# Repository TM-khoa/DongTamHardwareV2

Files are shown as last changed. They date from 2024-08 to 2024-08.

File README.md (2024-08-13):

# Hardware Air Cleaning Machine Valve Controller
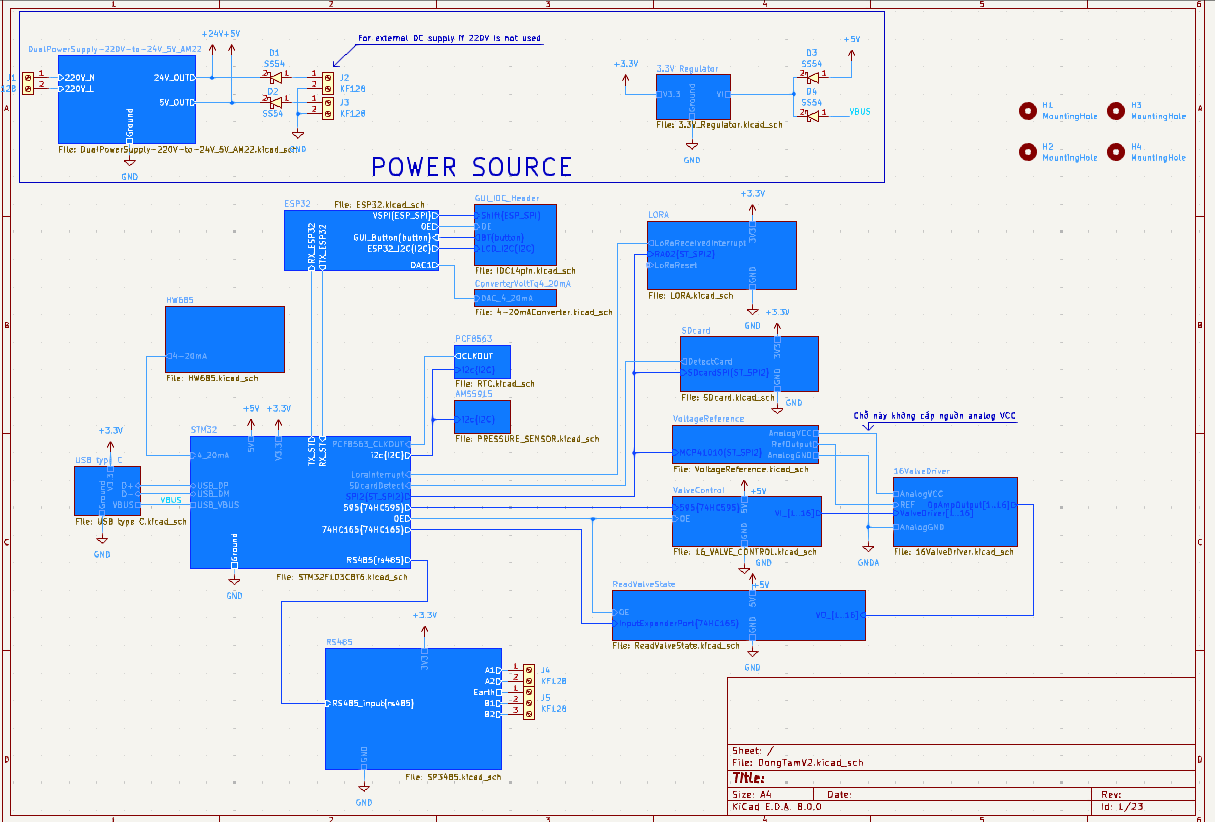
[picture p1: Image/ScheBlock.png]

# Hardware library

Download hardware library at this [repository](https://github.com/TM-khoa/KicadHardwareLibrary.git)
# Hardware description
## Powersource
- The system board is powered by a dual power supply, the AM22 AC-DC converter, which outputs both 24VDC and 5VDC.
- The power for the MCUs, LoRa module, and RS485 needs to be regulated to 3.3V using the LD1117-3.3 regulator.
- Other components can use the 5V output from the AM22.
- Two terminals—one for 5V and one for 24V—can be used to power the system board from an external DC supply.

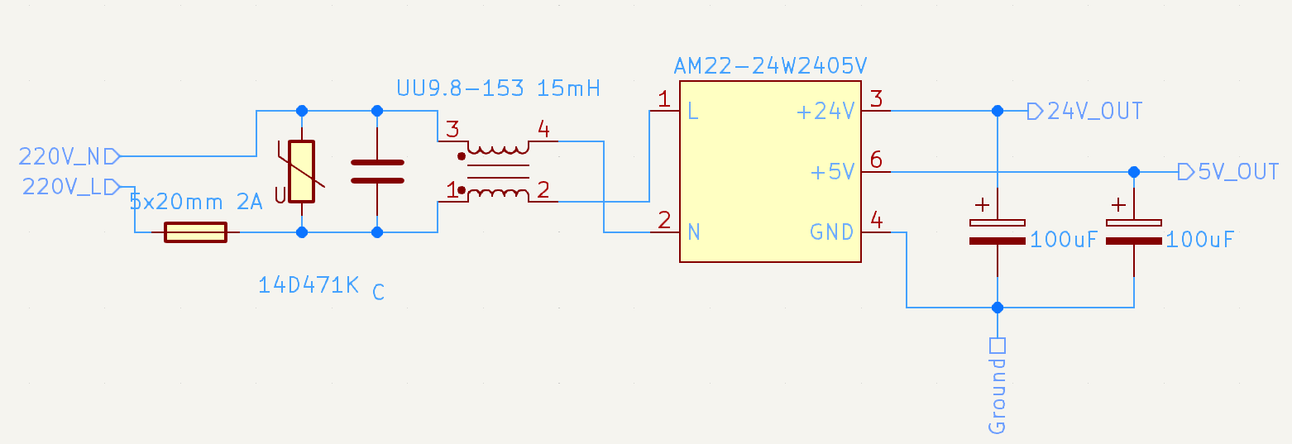
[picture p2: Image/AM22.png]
am22


## Control valve and fault detect
Each output pin of the Output Expander 74HC595 is connected to the Gate pin of an N-channel MOSFET (SI2302). The Source pin is connected to a 0.5 Ohm shunt resistor and to ground, while the Drain pin is connected to one terminal of the valve. The other valve terminal is connected to the 24V power supply.
	
An LM324 Op-Amp samples the voltage drop across the shunt resistor (approximately 300mV). This voltage is compared to a reference voltage to detect faults. A valve error occurs if there is no voltage drop.

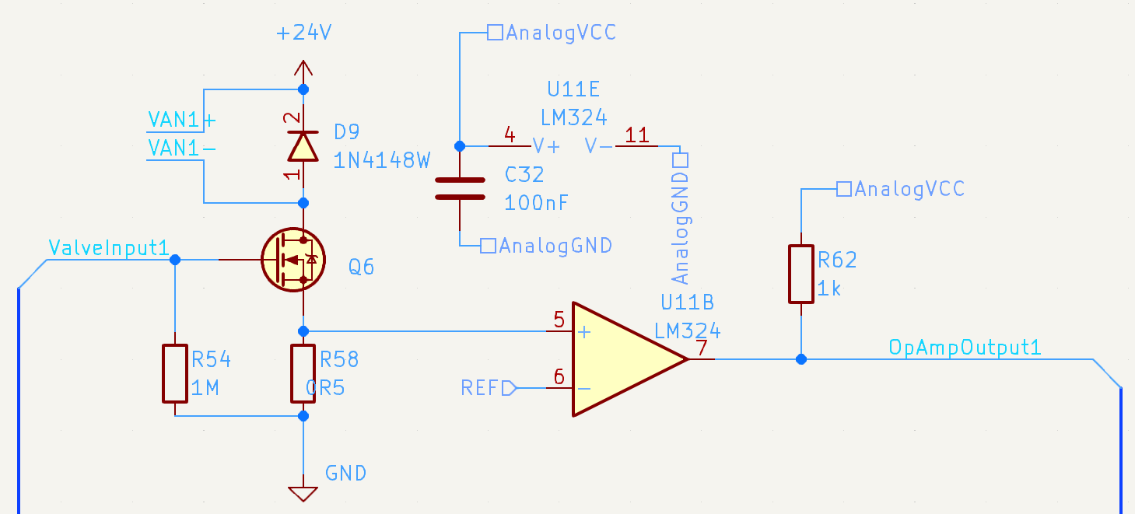
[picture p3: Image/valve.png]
valve


To control 16 valves, two cascaded 74HC595 output expanders are required, with each output pin equipped with an indicator LED.

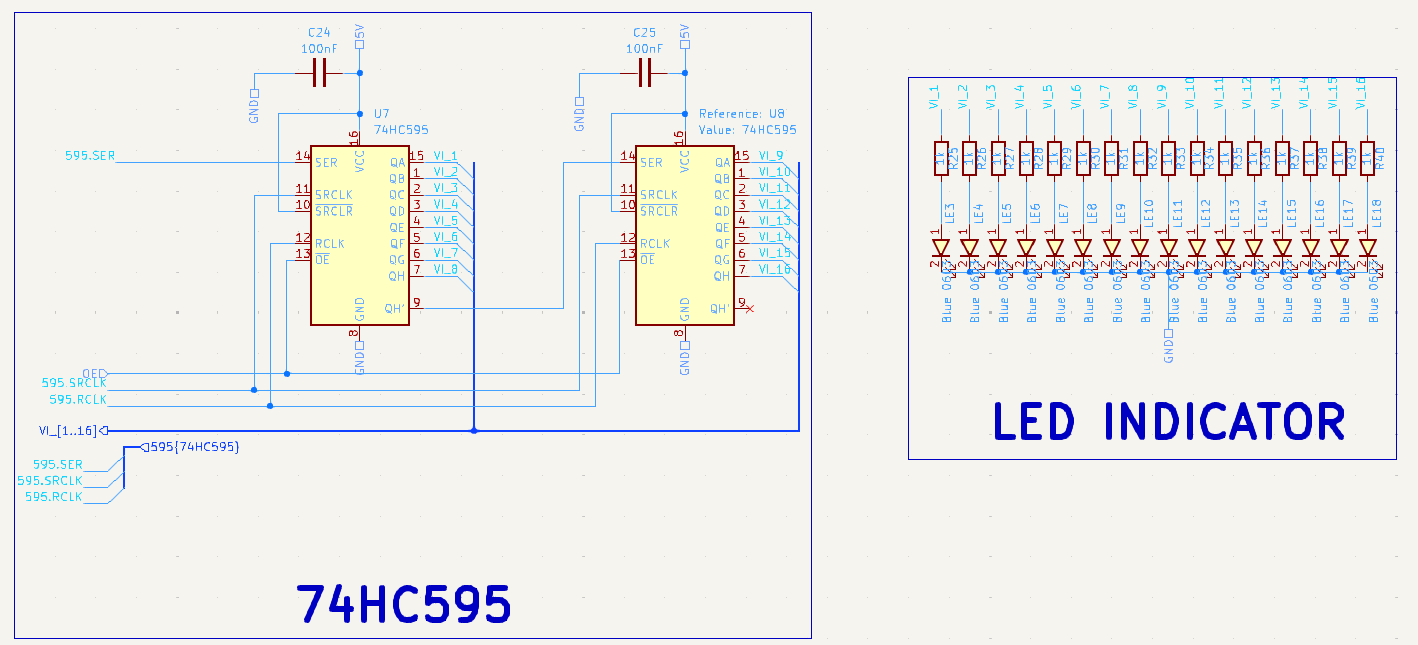
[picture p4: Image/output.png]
output


Each LM324 has four output pins, so four LM324 ICs are needed to monitor up to 16 valves. These outputs are connected to two cascaded 74HC165 input expanders and fed back to the MCU.

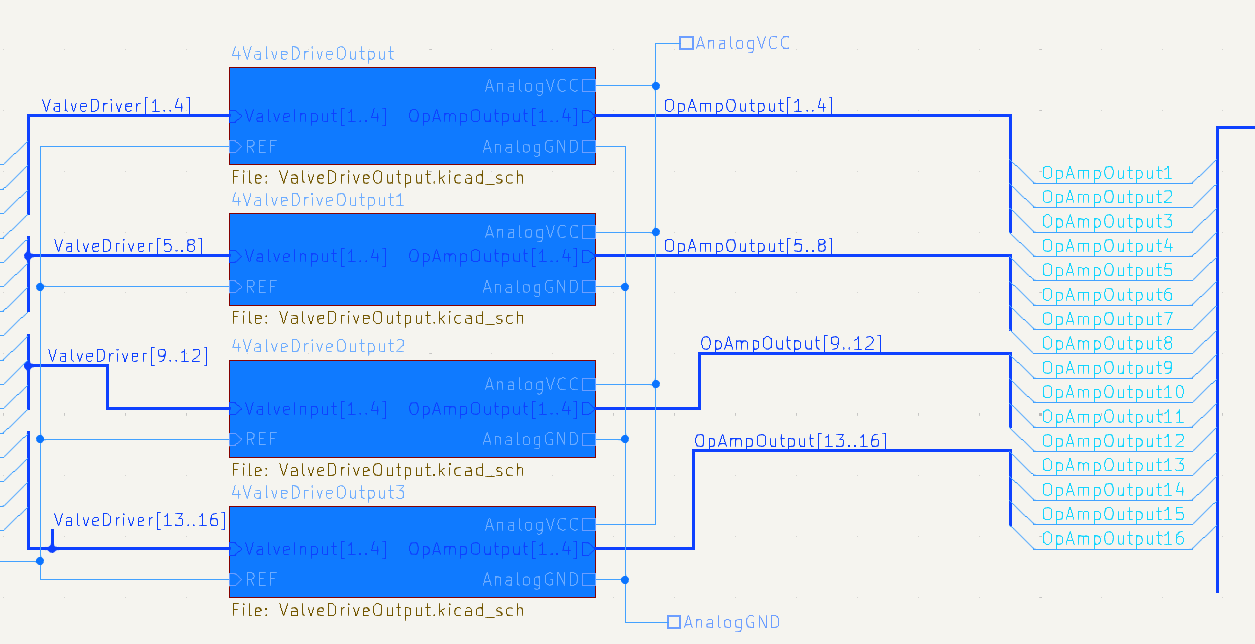
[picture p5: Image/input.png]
input


## Control LCD and LED bar

To interface the PCF8574 and 74HC595 pins (which require 5V at VIH) with the ESP32 (which outputs 3.3V at VOH), logic level shifters are needed on the I2C pins and the 74HC595 GPIO pins.

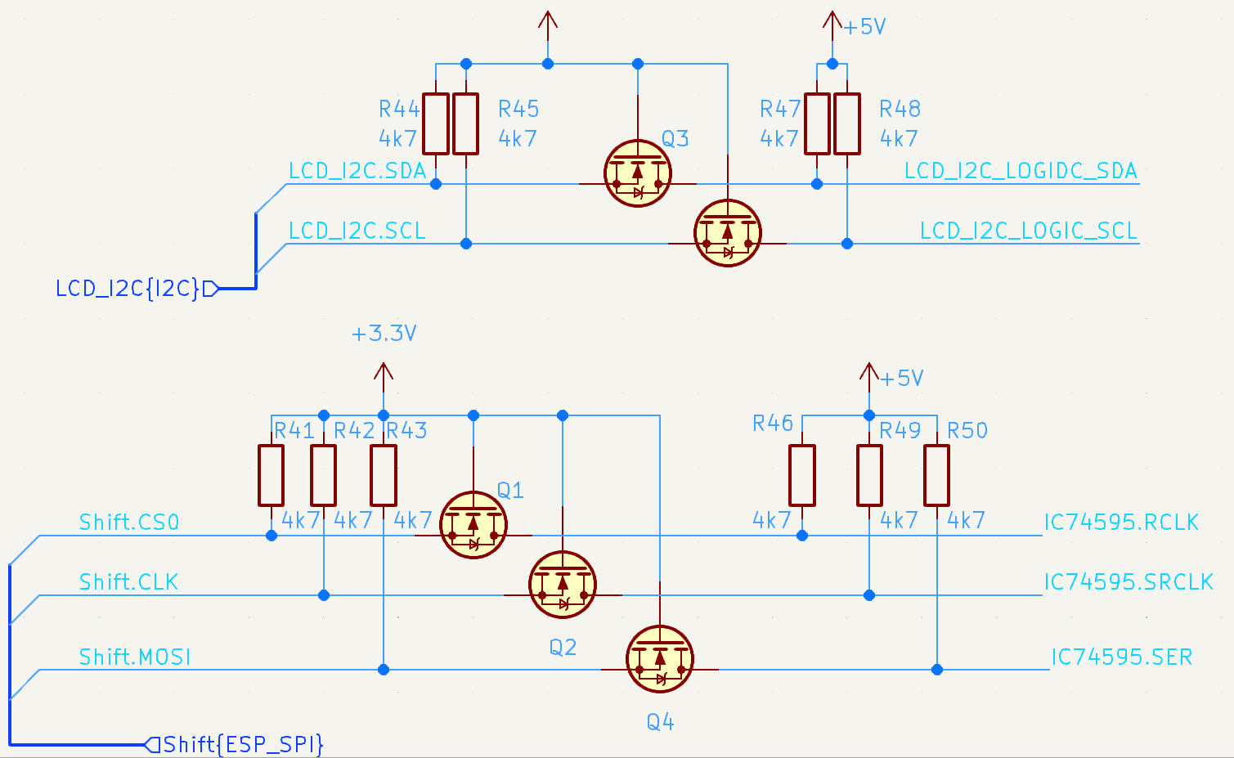
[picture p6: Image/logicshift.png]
logicshift
  

# STM32 pin table
| Pin Number | Pin Name | Function | Device | Description |
|---|---|---|---|---|
| 2 | PC13 | GPIO_OUTPUT | LED | |
| 3 | PC14 | GPIO_INTERRUPT | PCF8563 | Clock input interrupt |
| 18 | PB0 | GPIO_INTERRUPT | LORA RA-02  | LORA interrupt |
| 10 | PA0 | GPIO_OUTPUT | LORA RA-02  | SPI2 Chip select |
| 31 | PA10 | GPIO_OUTPUT | SDcard | SPI2 Chip select |
| 25 | PB12 | GPIO_OUTPUT | MCP41010 | SPI2 Chip select |
| 26 | PB13 | SPI2_SCK | LORA RA-02, Sdcard, MCP41010 | |
| 27 | PB14 | SPI2_MISO | | |
| 28 | PB15 | SPI2_MOSI | | |
| 21 | PB10 | UART3_TX | PC | Log output data to desktop |
| 22 | PB11 | UART3_RX | | |
| 45 | PB8 | I2C1_SCL | PCF8563, AMS5915 | |
| 46 | PB9 | I2C1_SDA | | |
| 42 | PB6 | USART1_TX | ESP32 | |
| 43 | PB7 | USART1_RX | | |
| 11 | PA1 | GPIO_OUTPUT | | |
| 12 | PA2 | USART2_TX | SP3485 | RS485 communicate |
| 13 | PA3 | USART2_RX | | |
| 32 | PA11 | USB_DM | USB-C port  | |
| 32 | PA12 | USB_DP | | |
| 15 | PA5 | GPIO_OUTPUT | 74HC595 | OutputExpander |
| 16 | PA6 | GPIO_OUTPUT | | |
| 17 | PA7 | GPIO_OUTPUT | | |
| 39 | PB3 | GPIO_OUTPUT | 74HC165 | InputExpander |
| 40 | PB4 | GPIO_OUTPUT | | |
| 41 | PB5 | GPIO_INPUT | | |
| 19 | PB1 | ADC | HW685 | Read pressure from SP100 |

# ESP32 pin table

| Pin Number | Pin Name | Function | Device | Description |
|---|---|---|---|---|
| 33 | IO21 | I2C_SDA | PCF8574 | LCD20x4 Output Expander |
| 36 | IO22 | I2C_SCL | | |
| 27 | IO16 | UART_RX | STM32 | |
| 28 | IO17 | UART_TX | | |
| 4 | IO36 | GPIO_INPUT | | Button from GUI user interface module |
| 5 | IO39 | GPIO_INPUT | | |
| 6 | IO34 | GPIO_INPUT | | |
| 7 | IO35 | GPIO_INPUT | | |
| 29 | IO5 | GPIO_OUTPUT| | |
| 30 | IO18 | SPI_CLK | 74HC595 | Control LED bar level |
| 31 | IO19 | SPI_MISO | | |
| 37 | IO23 | SPI_MOSI | | |

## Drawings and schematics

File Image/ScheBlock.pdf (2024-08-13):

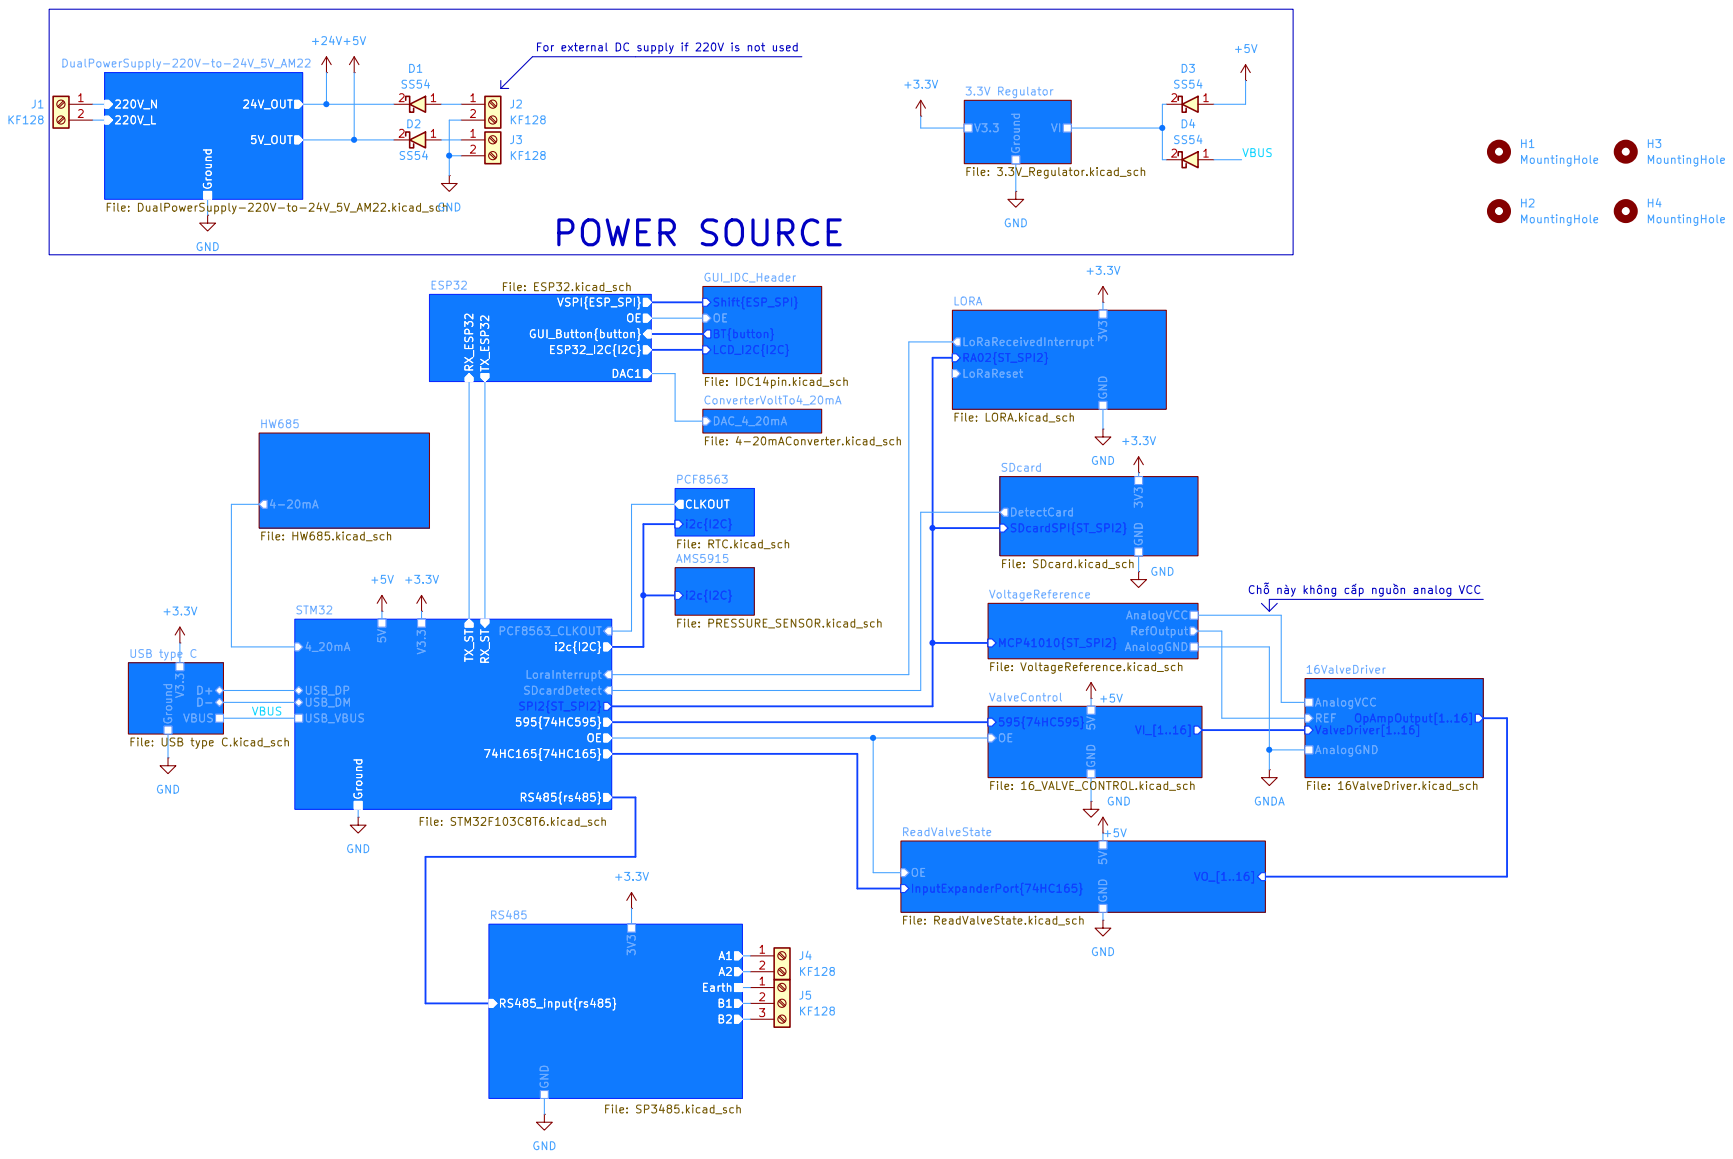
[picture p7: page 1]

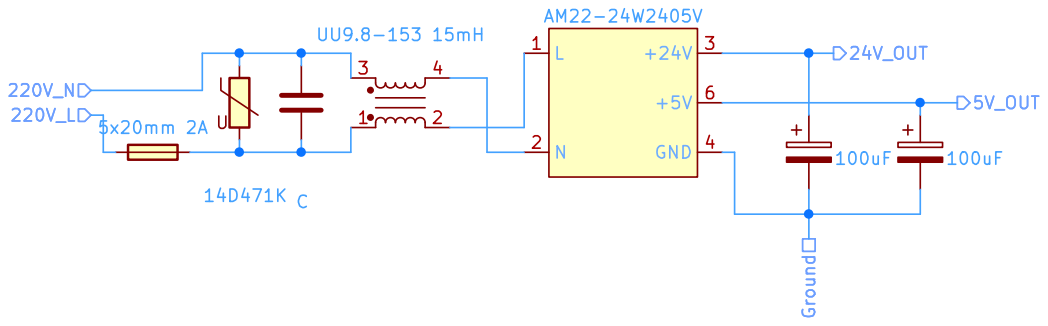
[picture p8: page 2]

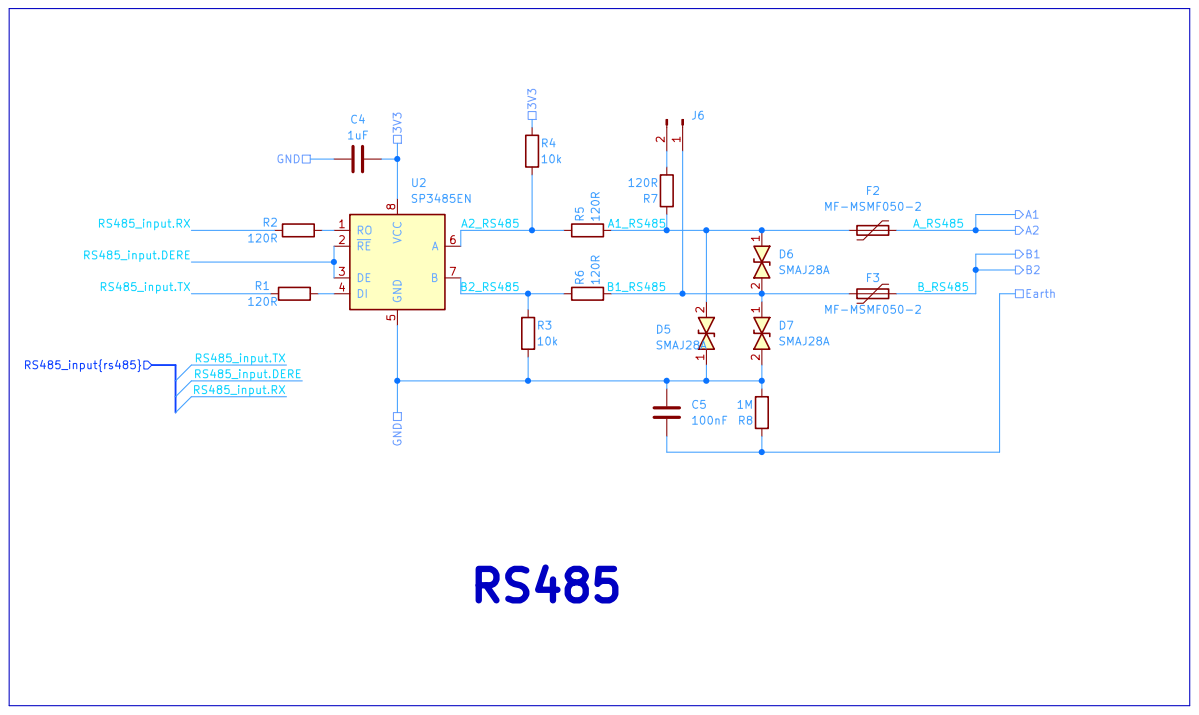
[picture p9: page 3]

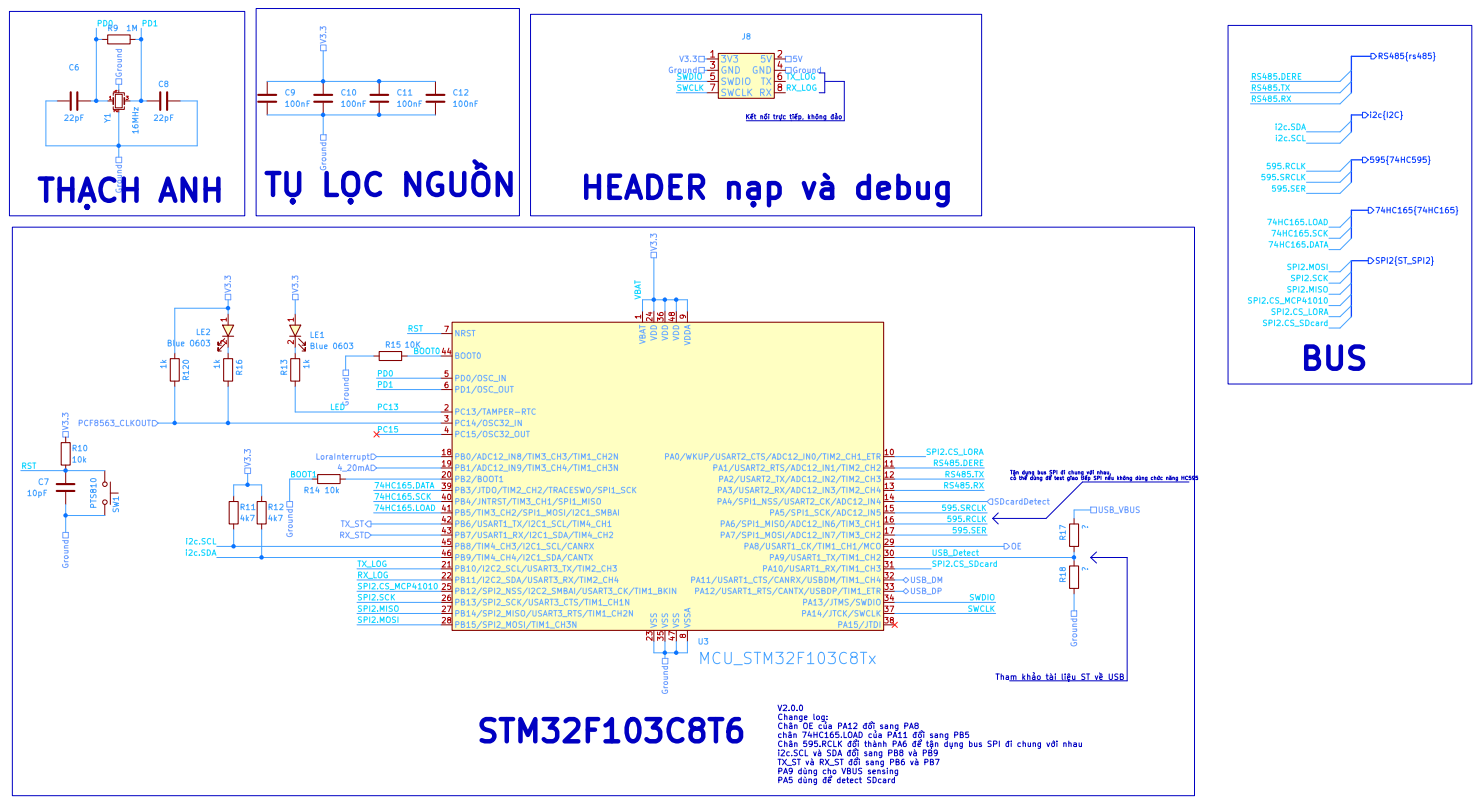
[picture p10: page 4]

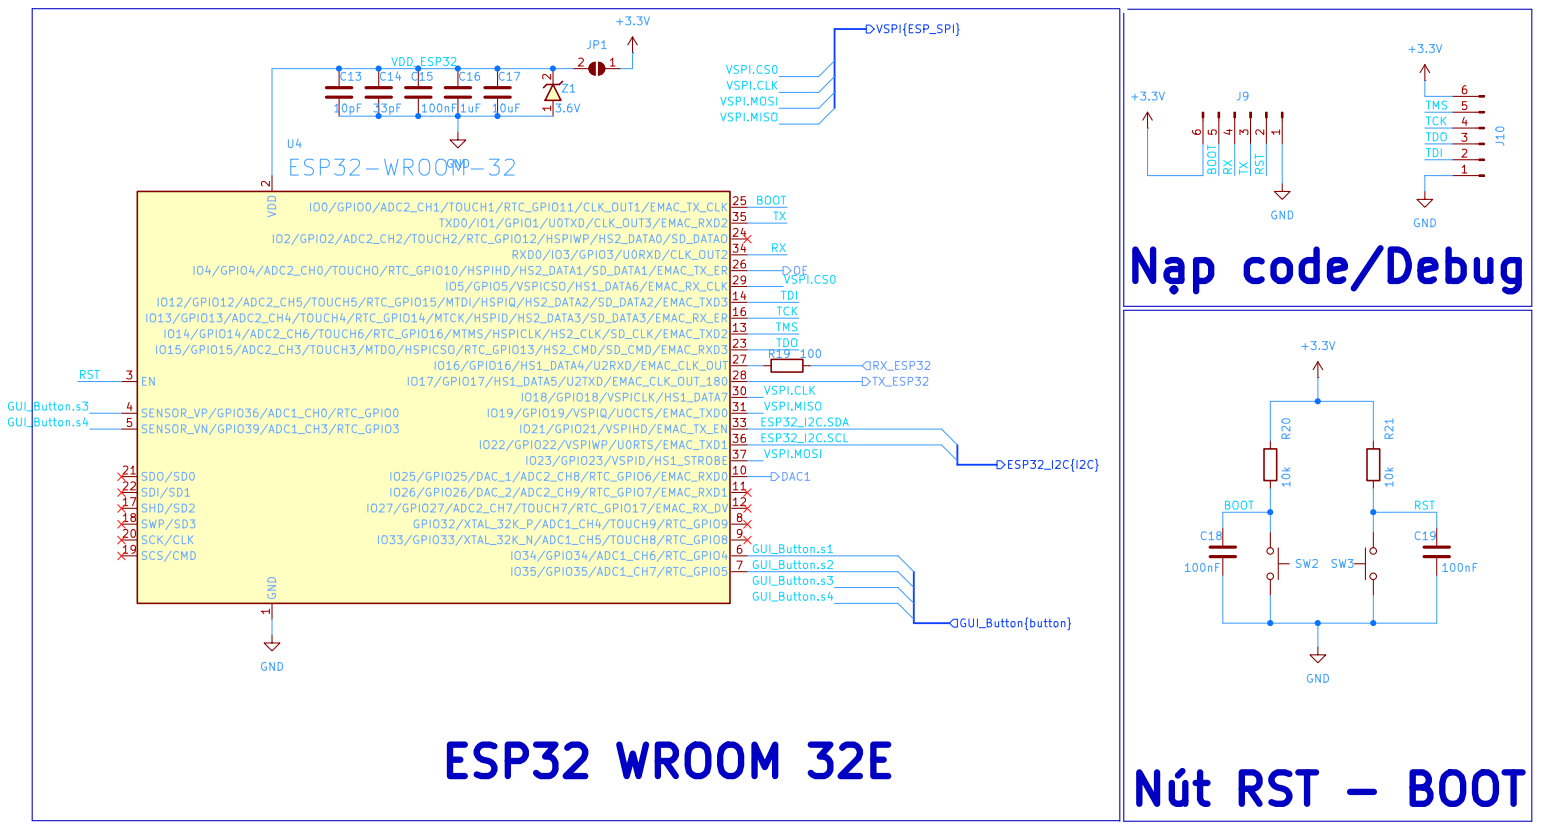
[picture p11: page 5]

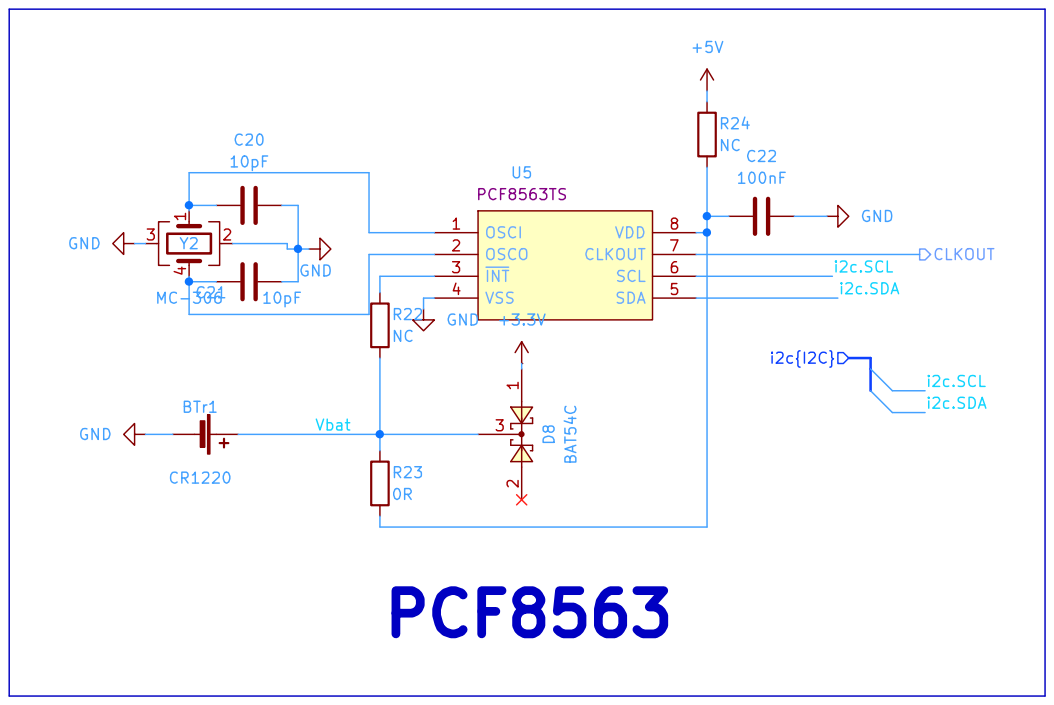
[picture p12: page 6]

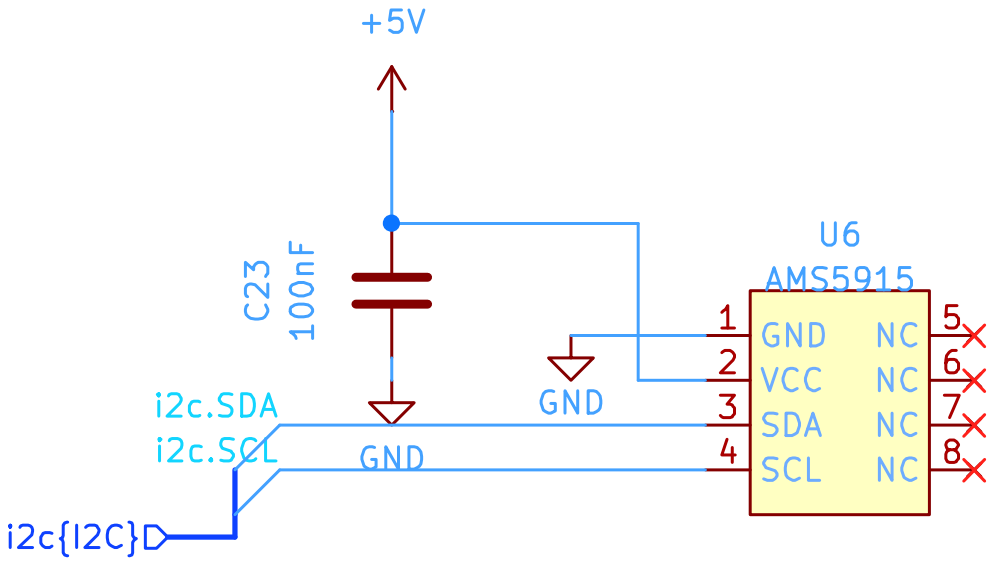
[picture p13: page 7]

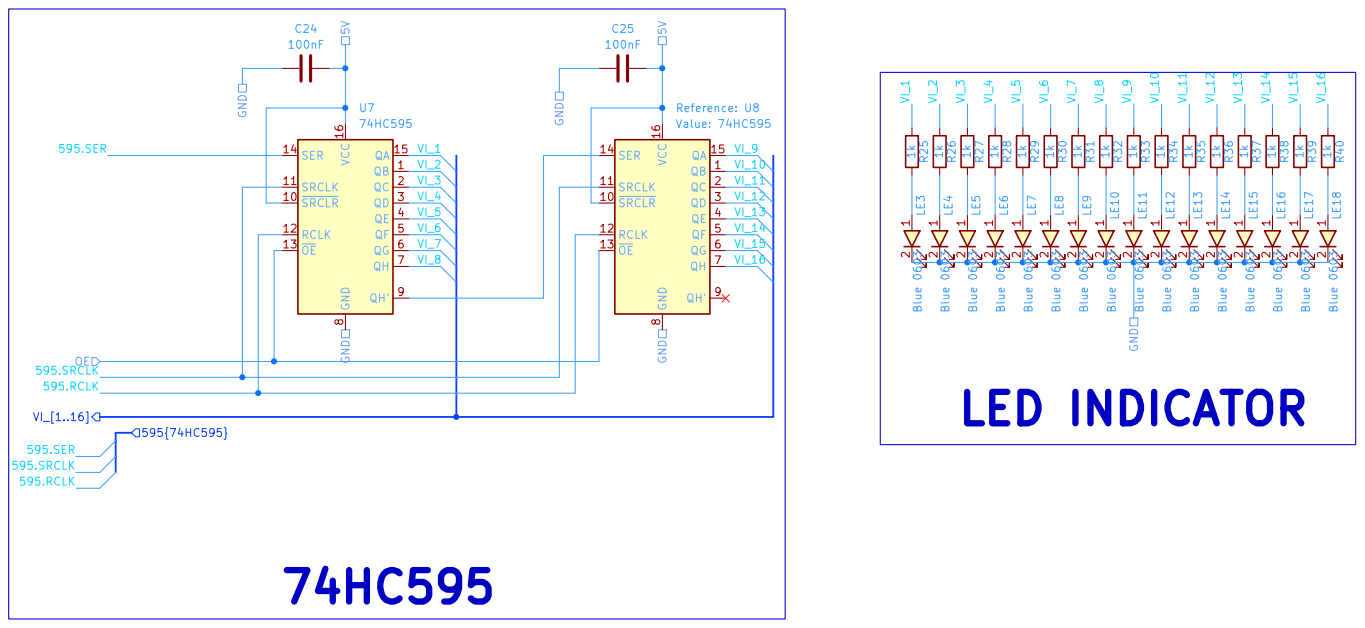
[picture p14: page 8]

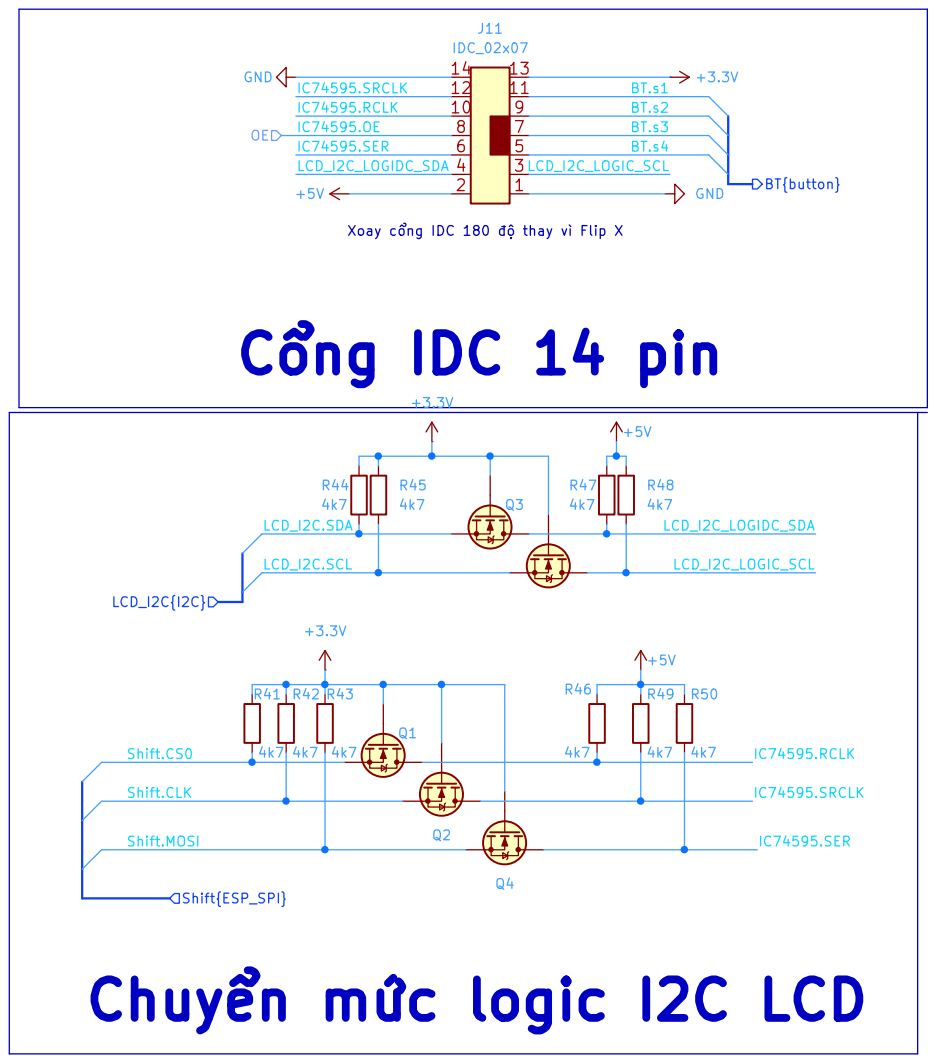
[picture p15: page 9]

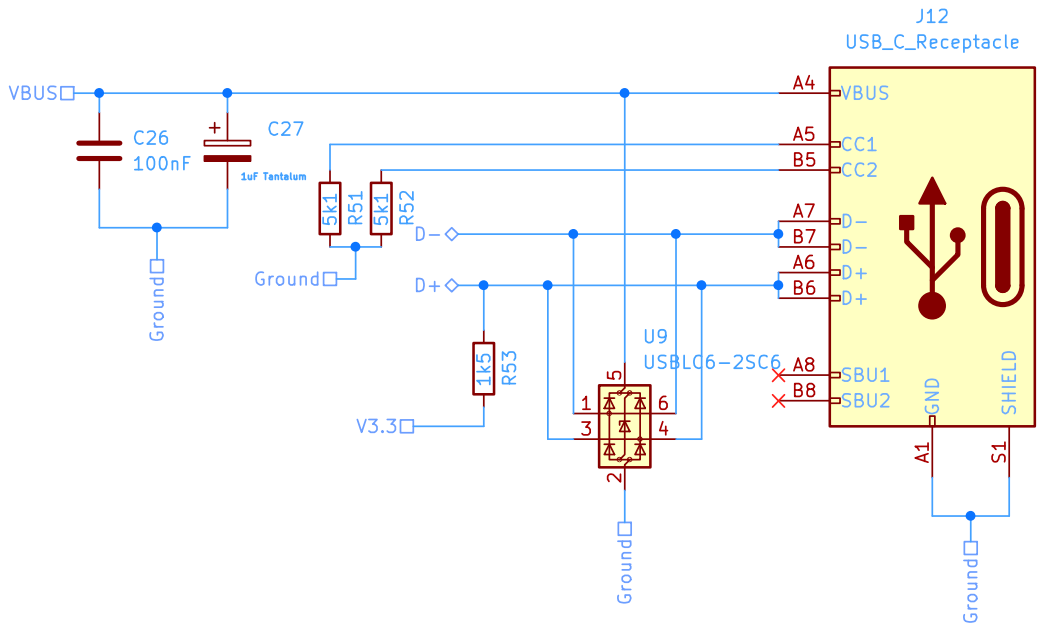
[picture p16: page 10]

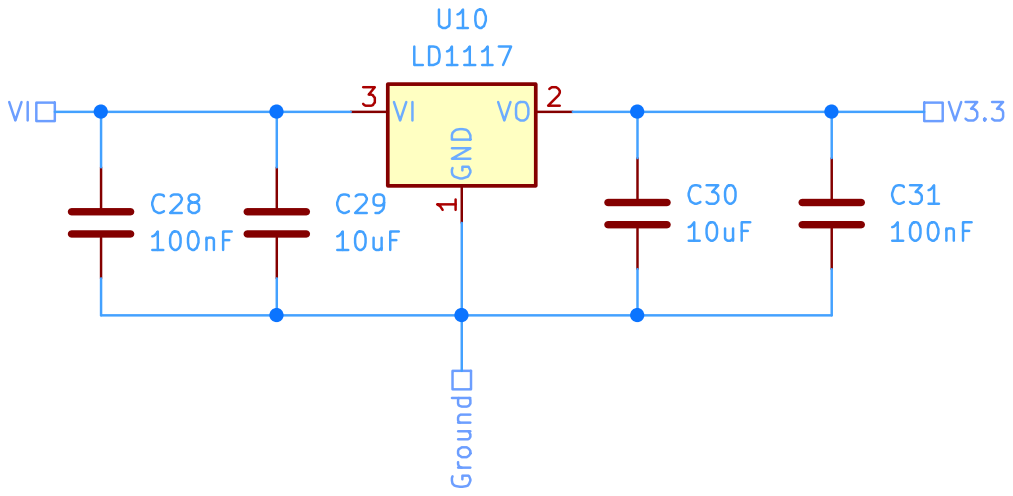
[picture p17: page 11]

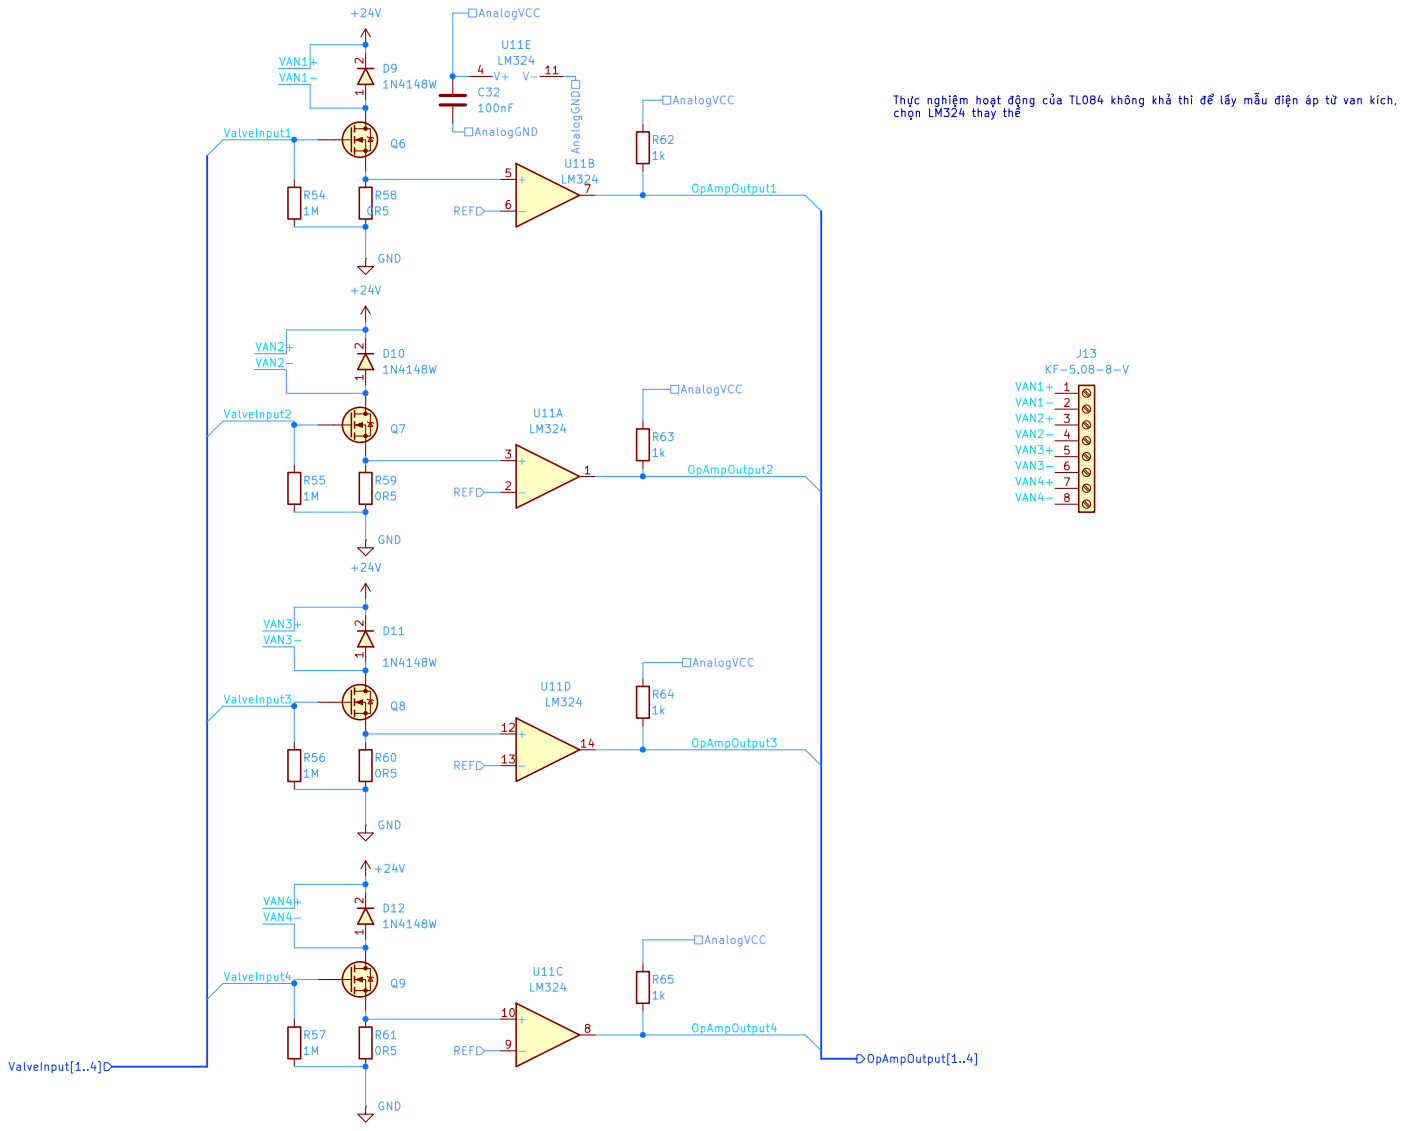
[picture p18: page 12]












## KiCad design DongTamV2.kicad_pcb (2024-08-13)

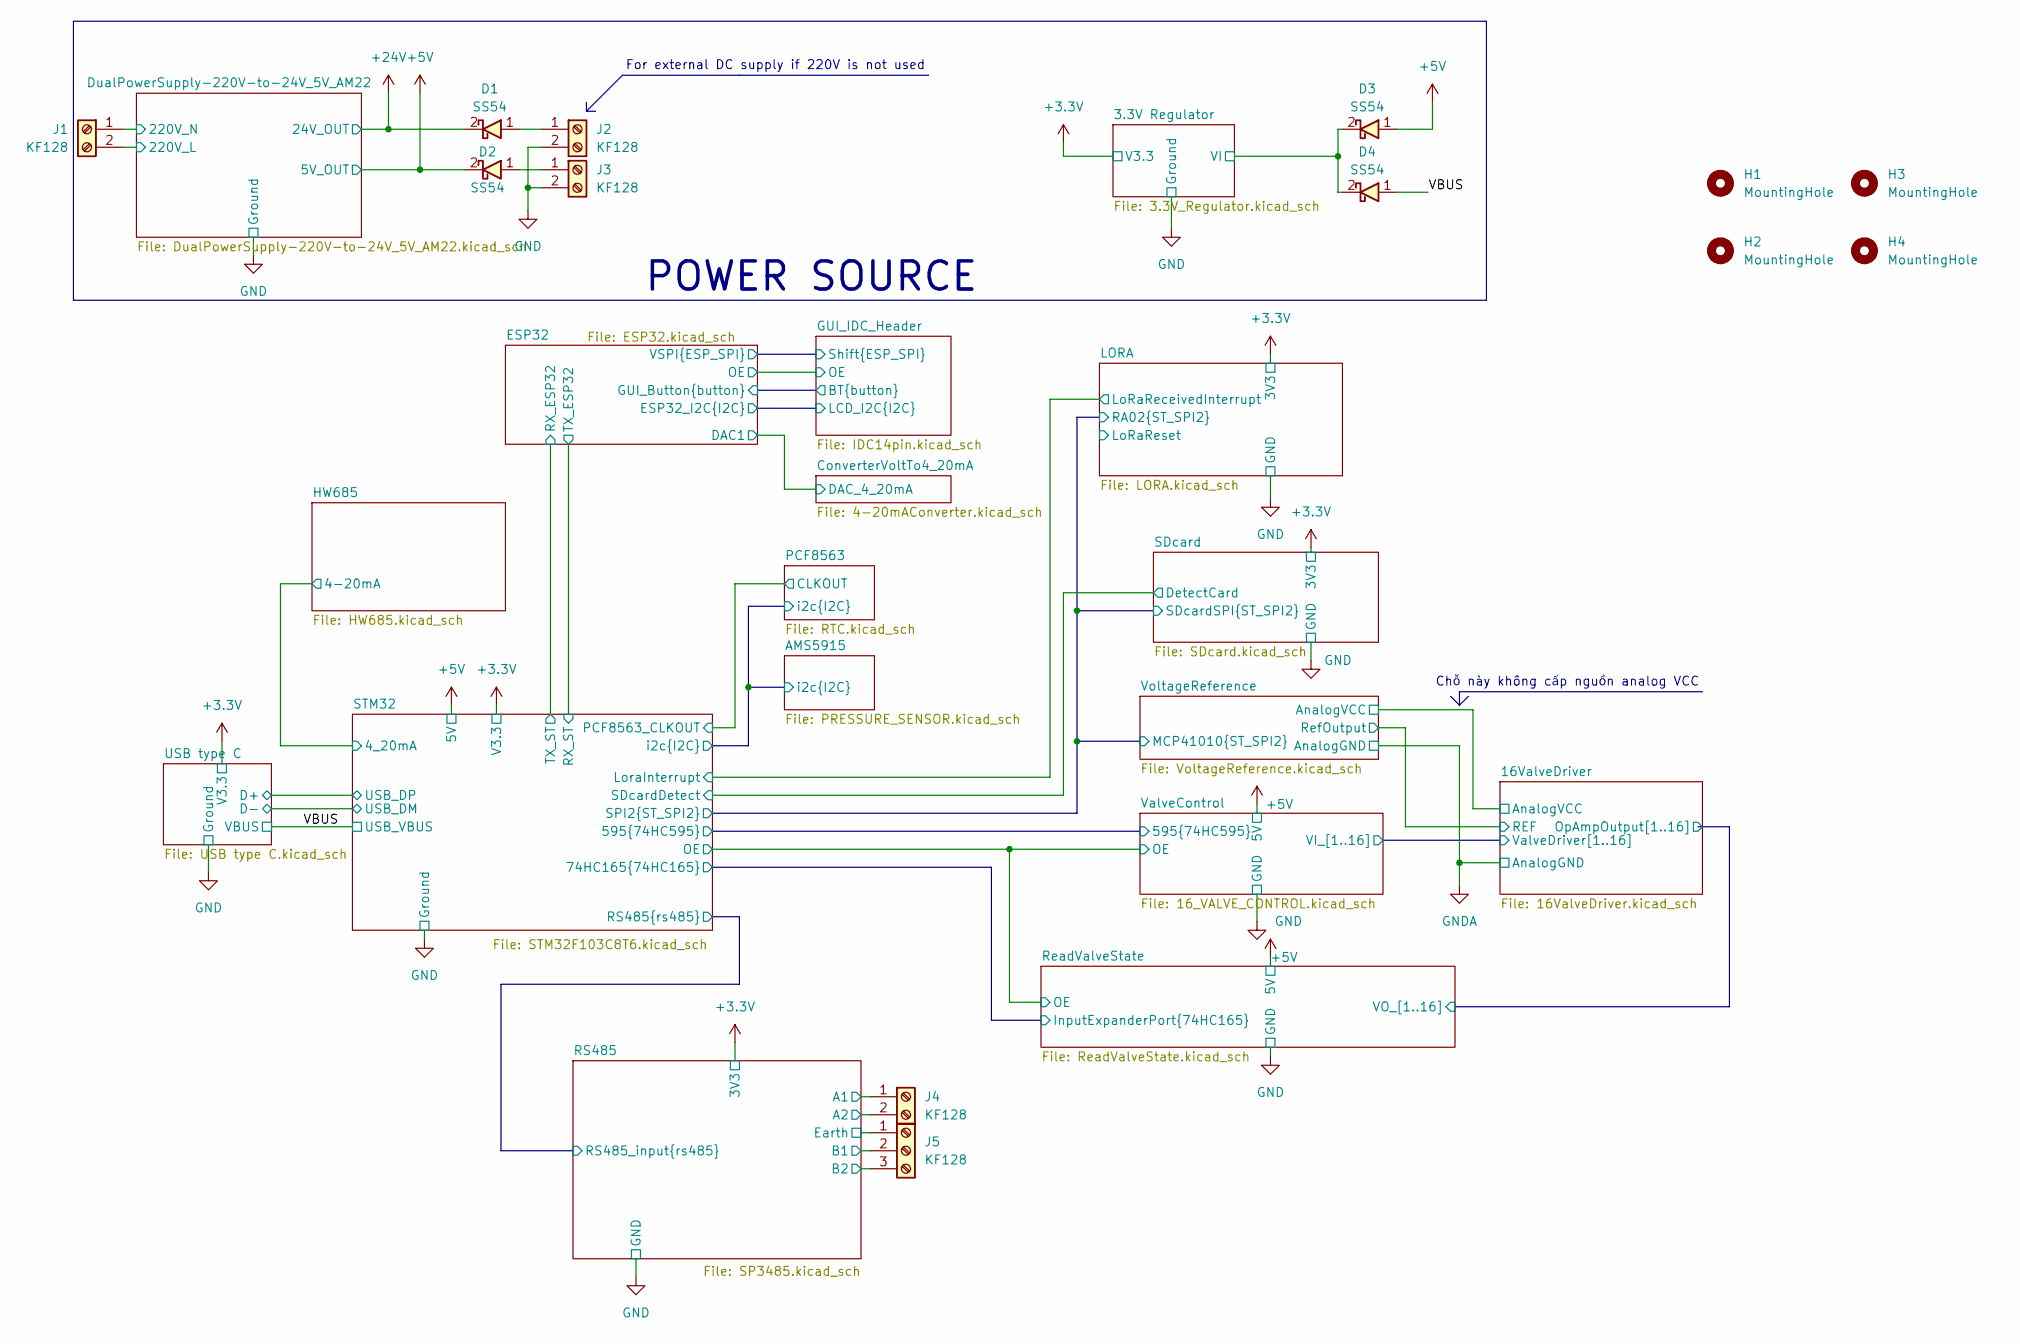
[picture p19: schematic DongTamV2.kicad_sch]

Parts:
D1, D2, D3, D4: SS54; Package-Diode-D_SMA
H1, H2, H3, H4: MountingHole; MountingHole_3.2mm_M3
J1, J2, J3, J4: KF128; TerminalBlock_bornier-2_P5.08mm
J5: KF128; TerminalBlock_bornier-3_P5.08mm

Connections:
+5V: D2.2, D3.1; also elsewhere on the board
+24V: D1.2; also elsewhere on the board
/3.3V Regulator/VI: D3.2, D4.2; also elsewhere on the board
/DualPowerSupply-220V-to-24V_5V_AM22/220V_L: J1.2; also elsewhere on the board
/DualPowerSupply-220V-to-24V_5V_AM22/220V_N: J1.1; also elsewhere on the board
/RS485/A_RS485: J4.1, J4.2; also elsewhere on the board
/RS485/B_RS485: J5.2, J5.3; also elsewhere on the board
/RS485/Earth: J5.1; also elsewhere on the board
/VBUS: D4.1; also elsewhere on the board
GND: J2.2, J3.2; also elsewhere on the board
unnamed: D1.1, J2.1
unnamed: D2.1, J3.1

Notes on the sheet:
POWER SOURCE
Chỗ này không cấp nguồn analog VCC
For external DC supply if 220V is not used

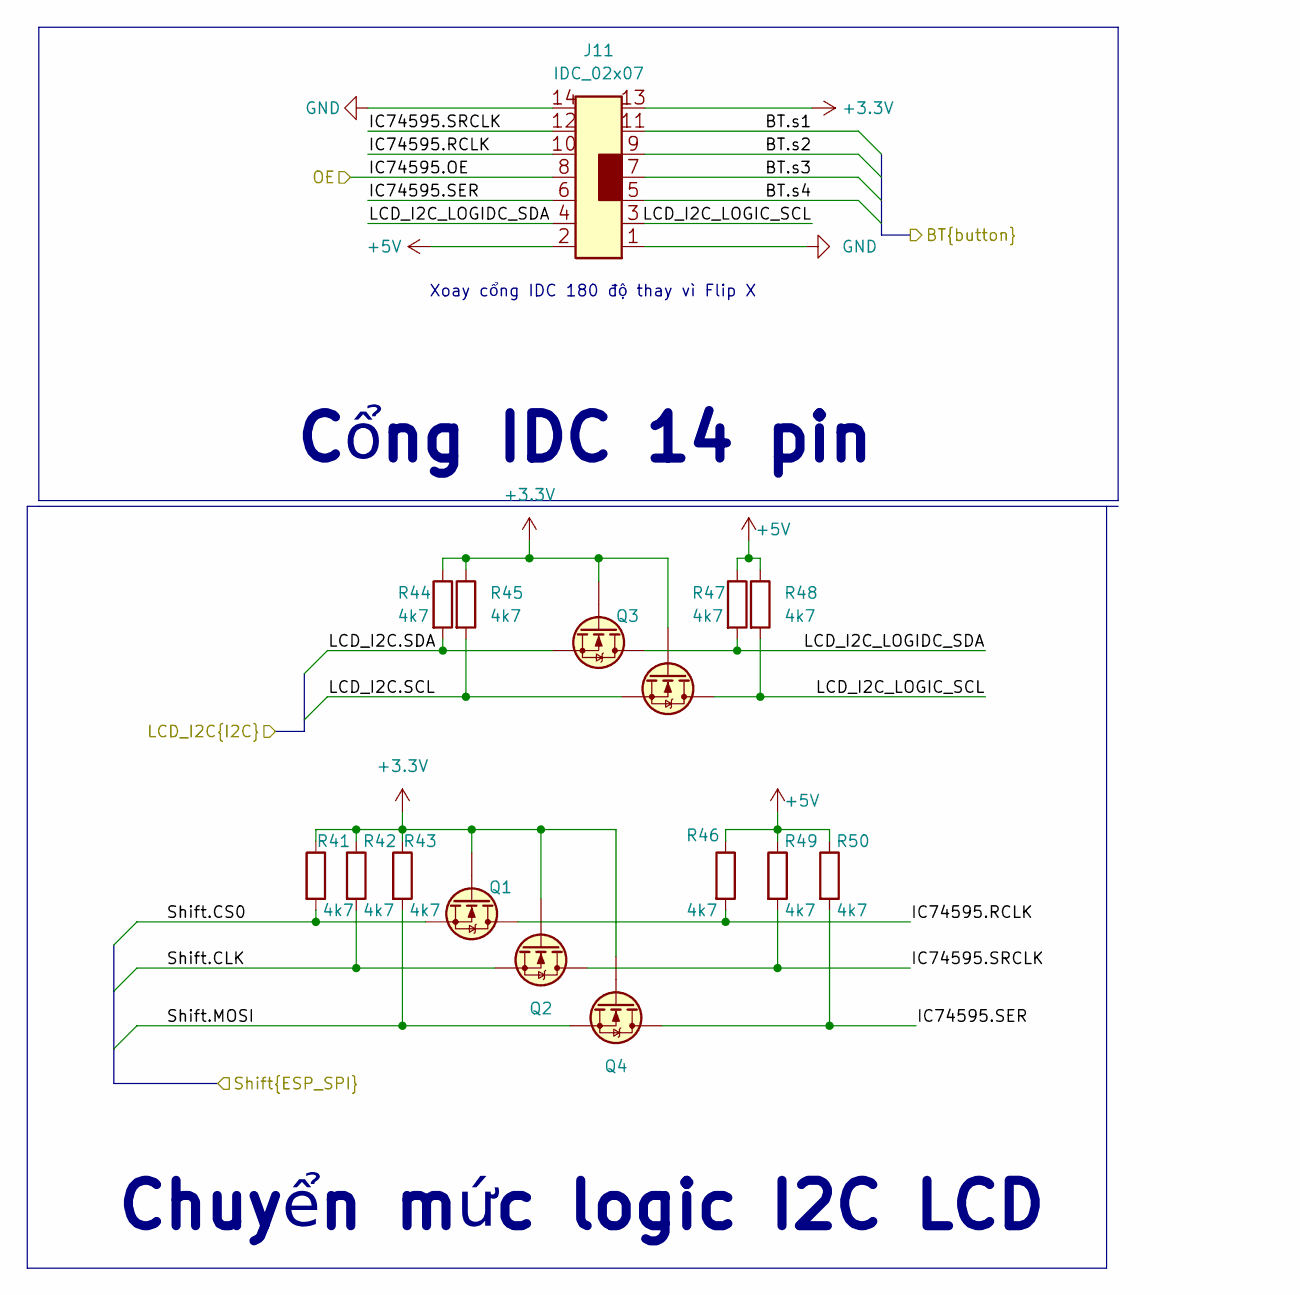
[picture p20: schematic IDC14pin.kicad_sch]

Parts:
J11: IDC_02x07; Conn-Vert-THT-2x7P-2.54mm-DC3
Q1, Q2, Q3, Q4, Q5: SI2302/BSS138; SOT23-3
R41, R42, R43, R44, R45, R46, R47, R48, R49, R50: 4k7; R_0603

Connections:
+3.3V: J11.13, Q1.1 (G), Q2.1 (G), Q3.1 (G), Q4.1 (G), Q5.1 (G), R41.1, R42.1, R43.1, R44.1, R45.1; also elsewhere on the board
+5V: J11.2, R46.1, R47.1, R48.1, R49.1, R50.1; also elsewhere on the board
/ESP32/ESP32_I2C.SCL: Q5.2 (S), R45.2; also elsewhere on the board
/ESP32/ESP32_I2C.SDA: Q3.2 (S), R44.2; also elsewhere on the board
/ESP32/GUI_Button.s1: J11.11; also elsewhere on the board
/ESP32/GUI_Button.s2: J11.9; also elsewhere on the board
/ESP32/GUI_Button.s3: J11.7; also elsewhere on the board
/ESP32/GUI_Button.s4: J11.5; also elsewhere on the board
/ESP32/VSPI.CLK: Q2.2 (S), R42.2; also elsewhere on the board
/ESP32/VSPI.CS0: Q1.2 (S), R41.2; also elsewhere on the board
/ESP32/VSPI.MOSI: Q4.2 (S), R43.2; also elsewhere on the board
/GUI_IDC_Header/IC74595.OE: J11.8; also elsewhere on the board
/GUI_IDC_Header/IC74595.RCLK: J11.10, Q1.3 (D), R46.2
/GUI_IDC_Header/IC74595.SER: J11.6, Q4.3 (D), R50.2
/GUI_IDC_Header/IC74595.SRCLK: J11.12, Q2.3 (D), R49.2
/GUI_IDC_Header/LCD_I2C_LOGIC_SCL: J11.3, Q5.3 (D), R48.2
/GUI_IDC_Header/LCD_I2C_LOGIDC_SDA: J11.4, Q3.3 (D), R47.2
GND: J11.1, J11.14; also elsewhere on the board

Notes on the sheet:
Chuyển mức logic I2C LCD
Xoay cổng IDC 180 độ thay vì Flip X
Cổng IDC 14 pin

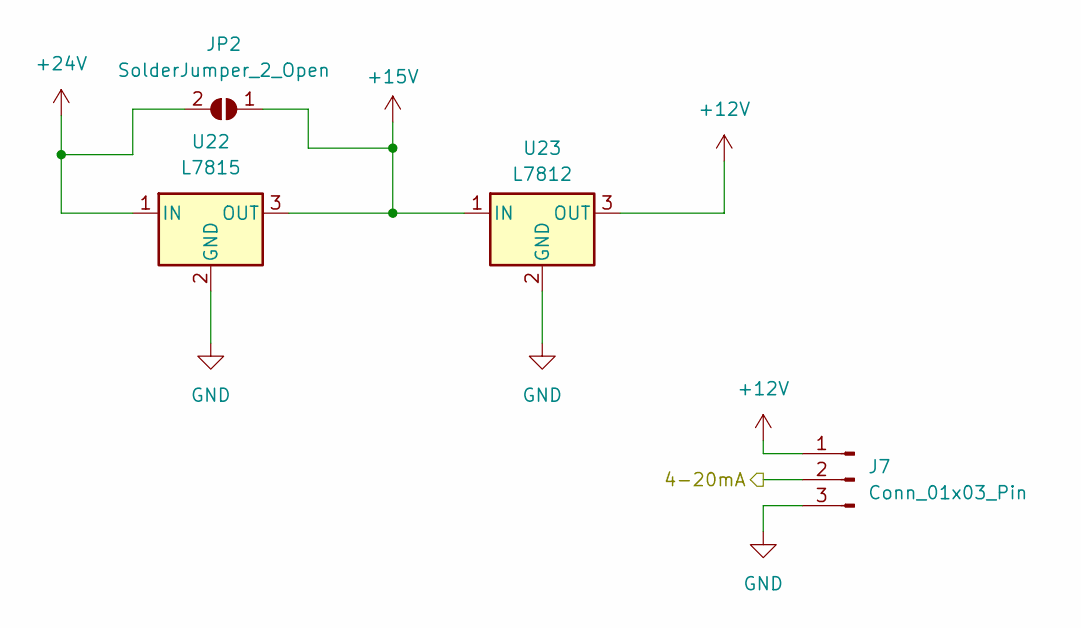
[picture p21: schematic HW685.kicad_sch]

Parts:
J7: Conn_01x03_Pin; PinHeader_1x03_P2.54mm_Vertical
JP2: SolderJumper_2_Open; SolderJumper-2_P1.3mm_Open_TrianglePad1.0x1.5mm
U22: L7815; Package-IC-Vert-SMD-TO_263-2_TabPin2
U23: L7812; Package-IC-Vert-SMD-TO_263-2_TabPin2

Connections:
+12V: J7.1, U23.3 (OUT)
+15V: JP2.1 (A), U22.3 (OUT), U23.1 (IN)
+24V: JP2.2 (B), U22.1 (IN); also elsewhere on the board
/HW685/4-20mA: J7.2; also elsewhere on the board
GND: J7.3, U22.2 (GND), U23.2 (GND); also elsewhere on the board

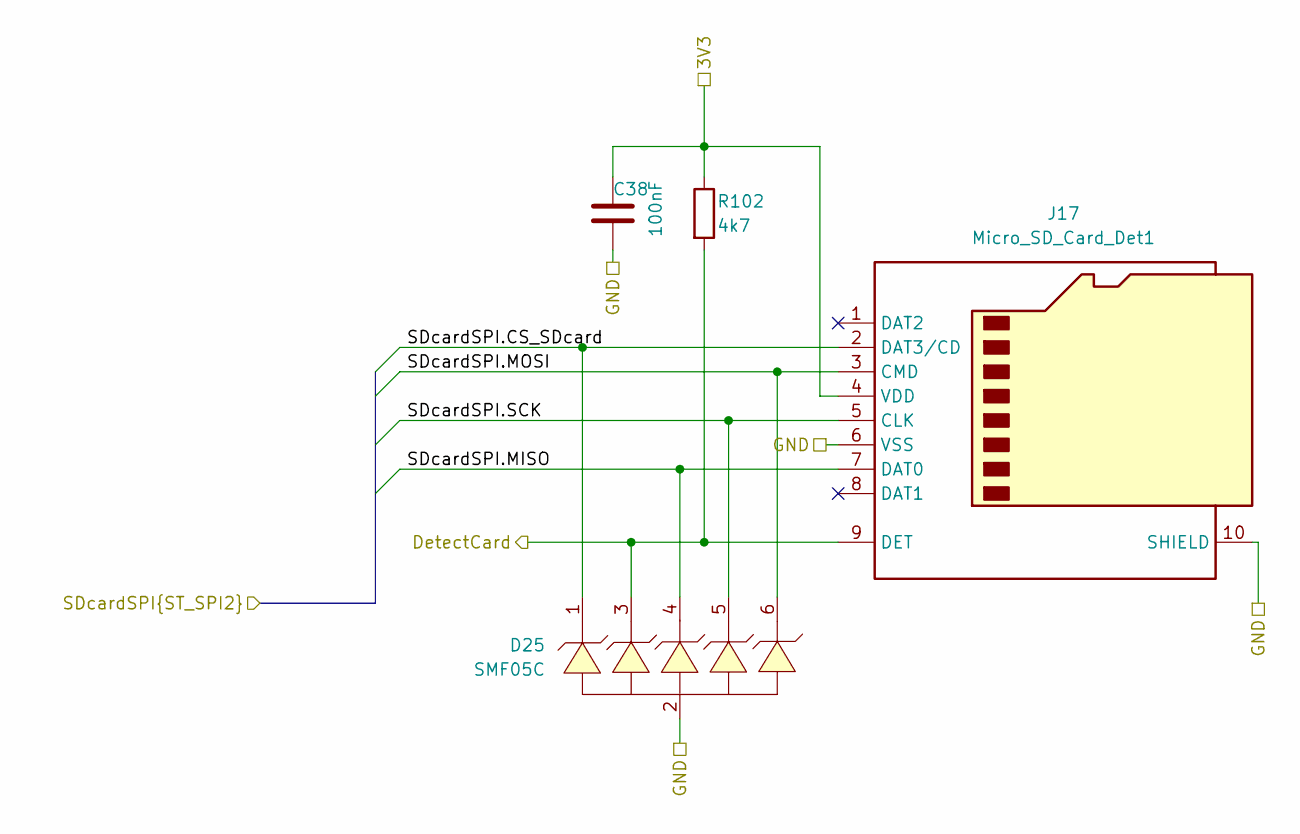
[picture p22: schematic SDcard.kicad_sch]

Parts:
C38: 100nF; C_0603
D25: SMF05C; Package-IC-TSSOP_6
J17: Micro_SD_Card_Det1; Socket_MicroSD-9P
R102: 4k7; R_0603

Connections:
+3.3V: C38.1, J17.4 (VDD), R102.1; also elsewhere on the board
/LORA/RA02.CS_SDcard: D25.1, J17.2 (DAT3/CD); also elsewhere on the board
/LORA/RA02.MISO: D25.4, J17.7 (DAT0); also elsewhere on the board
/LORA/RA02.MOSI: D25.6, J17.3 (CMD); also elsewhere on the board
/LORA/RA02.SCK: D25.5, J17.5 (CLK); also elsewhere on the board
/SDcard/DetectCard: D25.3, J17.9 (DET), R102.2; also elsewhere on the board
GND: C38.2, D25.2, J17.6 (VSS), J17.10 (SHIELD); also elsewhere on the board

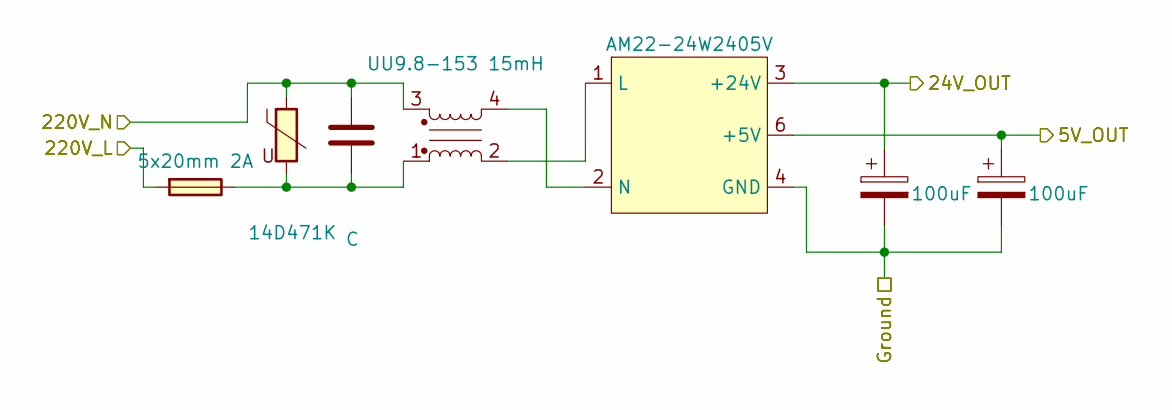
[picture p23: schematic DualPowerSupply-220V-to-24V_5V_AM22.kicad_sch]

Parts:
C1: C; C-Polyester-Rect-L16.5mm-W5.0mm-P15.00mm-MKT
C2, C3: 100uF; CP-Alu-SMD-8x10.5mm
F1: 5x20mm 2A; Fuse_BLX-A-P22.4mm
FL1: UU9.8-153 15mH; ACFilterChoke-UU9.8
RV1: 14D471K; RV_Disc_D12mm_W5.8mm_P7.5mm
U1: AM22-24W2405V; DualPowerSupply-24W_24V_05V_AM22

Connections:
+5V: C3.1, U1.6 (+5V); also elsewhere on the board
+24V: C2.1, U1.3 (+24V); also elsewhere on the board
/DualPowerSupply-220V-to-24V_5V_AM22/220V_L: F1.1; also elsewhere on the board
/DualPowerSupply-220V-to-24V_5V_AM22/220V_N: C1.1, FL1.3, RV1.1; also elsewhere on the board
GND: C2.2, C3.2, U1.4 (GND), U1.5 (GND); also elsewhere on the board
unnamed: C1.2, F1.2, FL1.1, RV1.2
unnamed: FL1.2, U1.1 (L)
unnamed: FL1.4, U1.2 (N)

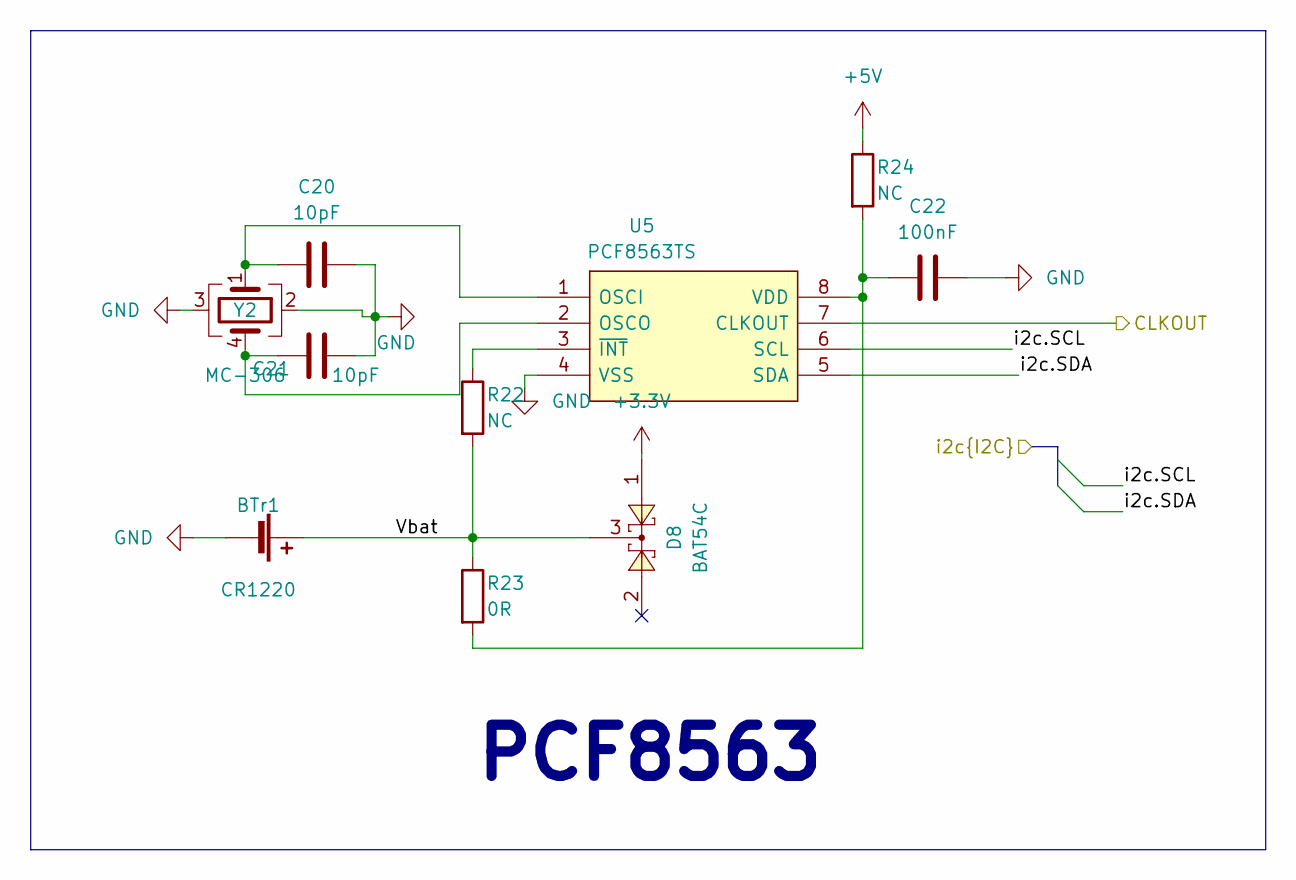
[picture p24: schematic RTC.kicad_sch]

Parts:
BTr1: CR1220; BatteryHolder-SMD-CR1220
C20, C21: 10pF; C_0603
C22: 100nF; C_0603
D8: BAT54C; SOT23-3
R22, R24: NC; R_0603
R23: 0R; R_0603
U5: PCF8563TS; Package-IC-Vert-SMD-1.27mm-8P-SOIC_8_Narrow_3.9x4.9mm; Mfg Part PCF8563TS/5,118
Y2: MC-306; Crystal_SMD_SeikoEpson_MC306-4Pin_8.0x3.2mm

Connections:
+3.3V: D8.1; also elsewhere on the board
+5V: R24.1; also elsewhere on the board
/AMS5915/i2c.SCL: U5.6 (SCL); also elsewhere on the board
/AMS5915/i2c.SDA: U5.5 (SDA); also elsewhere on the board
/PCF8563/CLKOUT: U5.7 (CLKOUT); also elsewhere on the board
/PCF8563/Vbat: BTr1.1 (+), D8.3, R22.2, R23.1
GND: BTr1.2 (-), C20.2, C21.2, C22.2, U5.4 (VSS), Y2.2, Y2.3; also elsewhere on the board
unnamed: C20.1, U5.1 (OSCI), Y2.1
unnamed: C21.1, U5.2 (OSCO), Y2.4
unnamed: C22.1, R23.2, R24.2, U5.8 (VDD)
unnamed: R22.1, U5.3 (~INT)

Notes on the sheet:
PCF8563

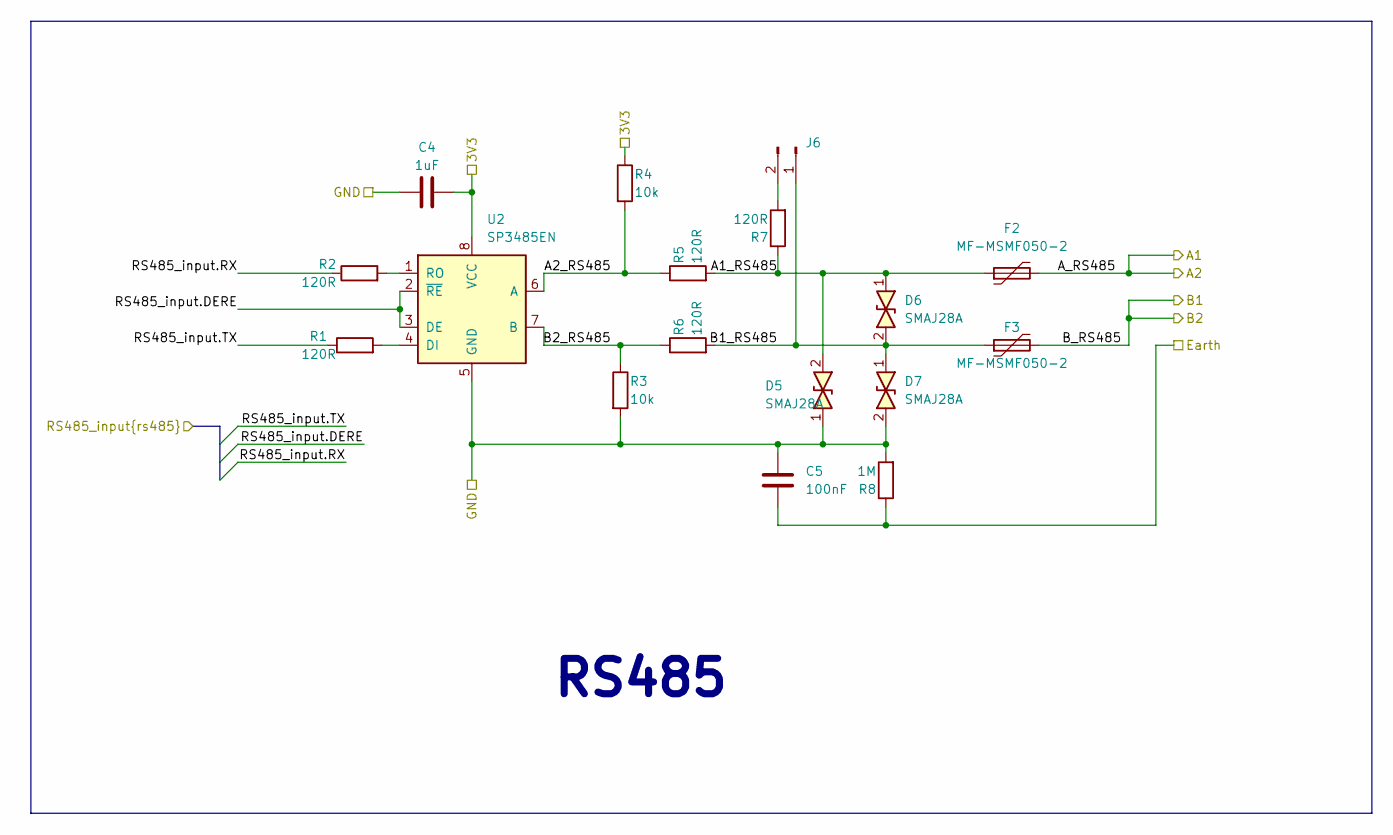
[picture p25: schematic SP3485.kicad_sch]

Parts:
C4: 1uF; C_0603
C5: 100nF; C_0603
D5, D6, D7: SMAJ28A; Package-Diode-D_SMA
F2, F3: MF-MSMF050-2; Fuse_1812_4532Metric
J6: Conn_01x02_Male; PinHeader_1x02_P2.54mm_Vertical
R1, R2, R5, R6, R7: 120R; R_0603
R3, R4: 10k; R_0603
R8: 1M; R_0603
U2: SP3485EN; Package-IC-Vert-SMD-1.27mm-8P-SOIC_8_Narrow_3.9x4.9mm

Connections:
+3.3V: C4.2, R4.1, U2.8 (VCC); also elsewhere on the board
/RS485/A1_RS485: D5.2, D6.1, F2.1, R5.2, R7.1
/RS485/A2_RS485: R4.2, R5.1, U2.6 (A)
/RS485/A_RS485: F2.2; also elsewhere on the board
/RS485/B1_RS485: D6.2, D7.1, F3.1, J6.1, R6.2
/RS485/B2_RS485: R3.1, R6.1, U2.7 (B)
/RS485/B_RS485: F3.2; also elsewhere on the board
/RS485/Earth: C5.1, R8.1; also elsewhere on the board
/RS485/RS485_input.DERE: U2.2 (~RE), U2.3 (DE); also elsewhere on the board
/RS485/RS485_input.RX: R2.1; also elsewhere on the board
/RS485/RS485_input.TX: R1.1; also elsewhere on the board
GND: C4.1, C5.2, D5.1, D7.2, R3.2, R8.2, U2.5 (GND); also elsewhere on the board
unnamed: J6.2, R7.2
unnamed: R1.2, U2.4 (DI)
unnamed: R2.2, U2.1 (RO)

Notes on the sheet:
RS485

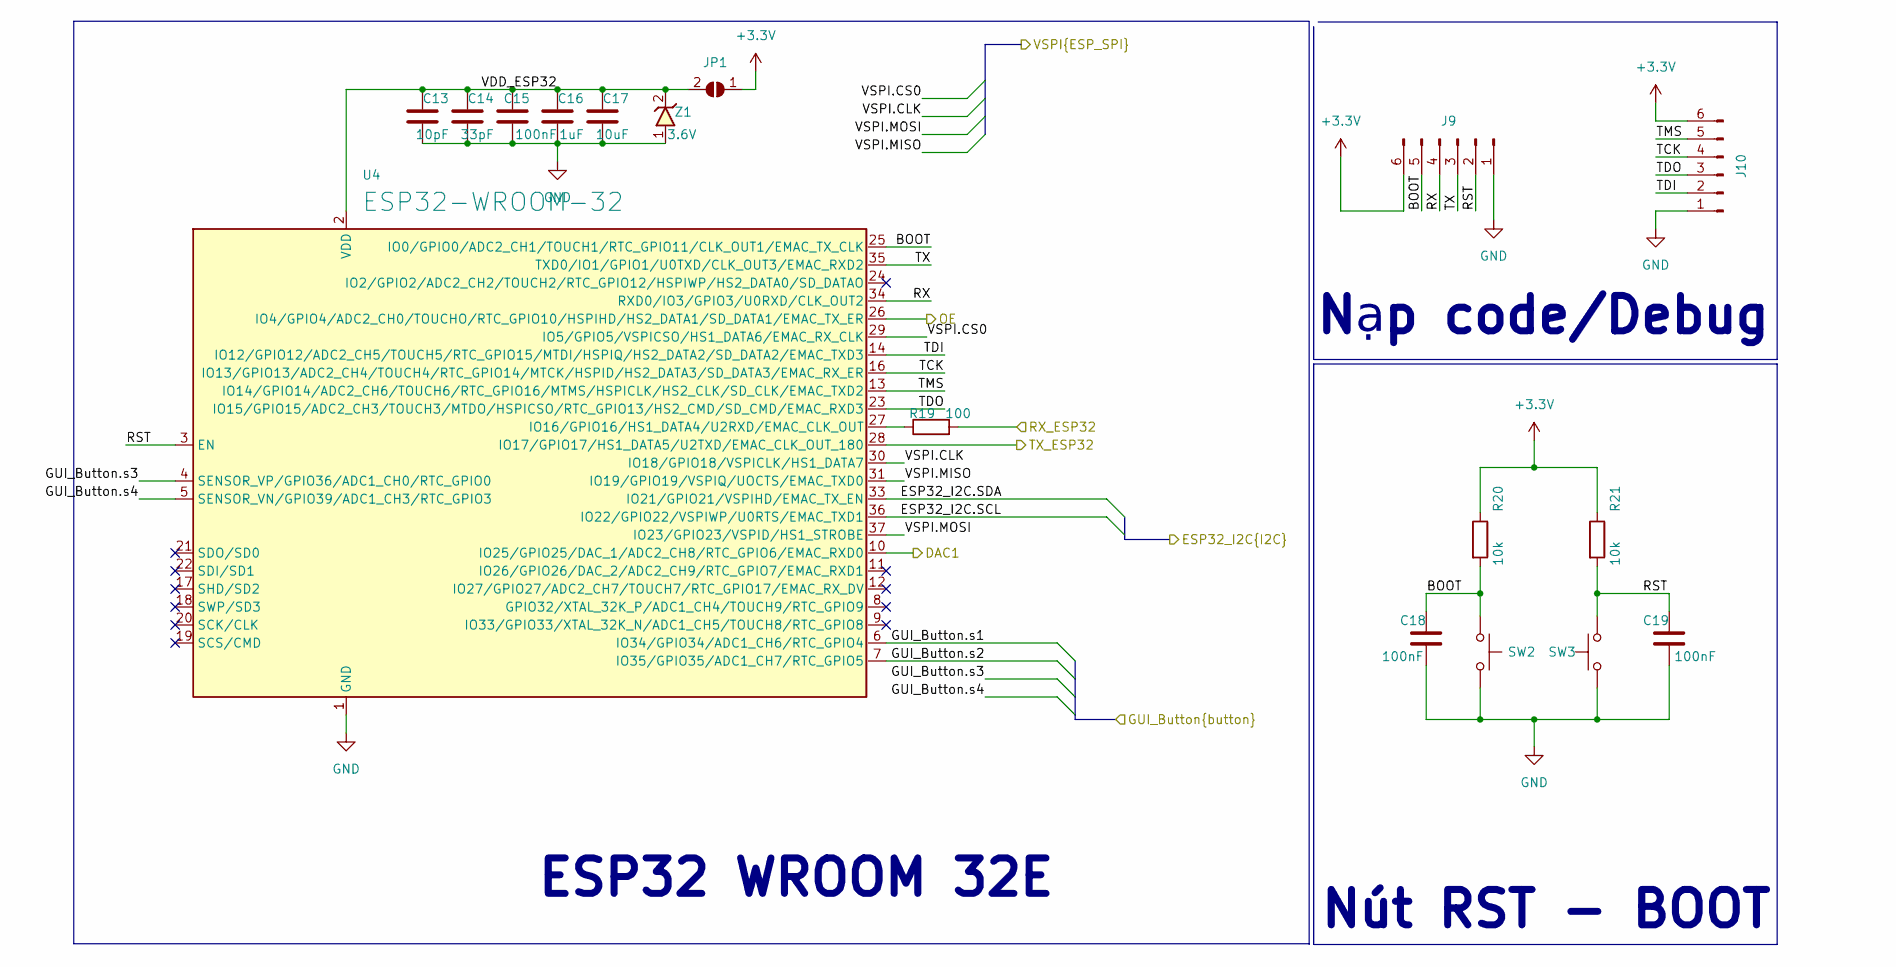
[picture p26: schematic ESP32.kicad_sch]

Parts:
C13: 10pF; C_0603
C14: 33pF; C_0603
C15, C18, C19: 100nF; C_0603
C16: 1uF; C_0603
C17: 10uF; C_0603
J9, J10: Conn_01x05_Male; PinHeader_1x06_P2.54mm_Vertical
JP1: SolderJumper-2_P1.3mm_Open_RoundedPad1.0x1.5mm
R19: 100; R_0603
R20, R21: 10k; R_0603
SW2, SW3: PTS810; ButtonPush-Vert-SMD-4P-SPST_PTS810
U4: ESP32-WROOM-32
Z1: 3.6V; Package-Diode-D_MiniMELF

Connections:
+3.3V: J9.6, J10.6, JP1.1 (A), R20.1, R21.1; also elsewhere on the board
/ConverterVoltTo4_20mA/DAC_4_20mA: U4.10 (IO25/GPIO25/DAC_1/ADC2_CH8/RTC_GPIO6/EM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); also elsewhere on the board
/ESP32/BOOT: C18.1, J9.5, R20.2, SW2.1, U4.25 (IO0/GPIO0/ADC2_CH1/TOUCH1/RTC_GPIO11/CL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)
/ESP32/ESP32_I2C.SCL: U4.36 (IO22/GPIO22/VSPIWP/U0RTS/EMAC_TXD1); also elsewhere on the board
/ESP32/ESP32_I2C.SDA: U4.33 (IO21/GPIO21/VSPIHD/EMAC_TX_EN); also elsewhere on the board
/ESP32/GUI_Button.s1: U4.6 (IO34/GPIO34/ADC1_CH6/RTC_GPIO4); also elsewhere on the board
/ESP32/GUI_Button.s2: U4.7 (IO35/GPIO35/ADC1_CH7/RTC_GPIO5); also elsewhere on the board
/ESP32/GUI_Button.s3: U4.4 (SENSOR_VP/GPIO36/ADC1_CH0/RTC_GPIO0); also elsewhere on the board
/ESP32/GUI_Button.s4: U4.5 (SENSOR_VN/GPIO39/ADC1_CH3/RTC_GPIO3); also elsewhere on the board
/ESP32/RST: C19.1, J9.2, R21.2, SW3.2, U4.3 (EN)
/ESP32/RX: J9.4, U4.34 (RXD0/IO3/GPIO3/U0RXD/CLK_OUT2)
/ESP32/RX_ESP32: R19.2; also elsewhere on the board
/ESP32/TCK: J10.4, U4.16 (IO13/GPIO13/ADC2_CH4/TOUCH4/RTC_GPIO14/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)
/ESP32/TDI: J10.2, U4.14 (IO12/GPIO12/ADC2_CH5/TOUCH5/RTC_GPIO15/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)
/ESP32/TDO: J10.3, U4.23 (IO15/GPIO15/ADC2_CH3/TOUCH3/MTDO/HSPICS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)
/ESP32/TMS: J10.5, U4.13 (IO14/GPIO14/ADC2_CH6/TOUCH6/RTC_GPIO16/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)
/ESP32/TX: J9.3, U4.35 (TXD0/IO1/GPIO1/U0TXD/CLK_OUT3/EMAC_RXD2)
/ESP32/TX_ESP32: U4.28 (IO17/GPIO17/HS1_DATA5/U2TXD/EMAC_CLK_OU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); also elsewhere on the board
/ESP32/VDD_ESP32: C13.1, C14.1, C15.1, C16.1, C17.1, JP1.2 (B), U4.2 (VDD), Z1.2
/ESP32/VSPI.CLK: U4.30 (IO18/GPIO18/VSPICLK/HS1_DATA7); also elsewhere on the board
/ESP32/VSPI.CS0: U4.29 (IO5/GPIO5/VSPICSO/HS1_DATA6/EMAC_RX_CLK); also elsewhere on the board
/ESP32/VSPI.MISO: U4.31 (IO19/GPIO19/VSPIQ/UOCTS/EMAC_TXD0)
/ESP32/VSPI.MOSI: U4.37 (IO23/GPIO23/VSPID/HS1_STROBE); also elsewhere on the board
/GUI_IDC_Header/IC74595.OE: U4.26 (IO4/GPIO4/ADC2_CH0/TOUCHO/RTC_GPIO10/HS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); also elsewhere on the board
GND: C13.2, C14.2, C15.2, C16.2, C17.2, C18.2, C19.2, J9.1, J10.1, SW2.2, SW3.1, U4.1 (GND), U4.15 (GND), U4.38 (GND), U4.39 (GND), Z1.1; also elsewhere on the board
unnamed: R19.1, U4.27 (IO16/GPIO16/HS1_DATA4/U2RXD/EMAC_CLK_OUT)

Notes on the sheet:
ESP32 WROOM 32E
Nạp code/Debug
Nút RST - BOOT

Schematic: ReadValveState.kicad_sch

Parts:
C36, C37: 100nF; C_0603
U15, U16: 74HC165; Package-IC-Vert-SMD-1.27mm-16P-SOIC_16_Narrow_3.92x10.2mm

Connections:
+5V: C36.2, C37.2, U15.16 (VCC), U16.16 (VCC); also elsewhere on the board
/16ValveDriver/OpAmpOutput1: U16.11 (D0); also elsewhere on the board
/16ValveDriver/OpAmpOutput2: U16.12 (D1); also elsewhere on the board
/16ValveDriver/OpAmpOutput3: U16.13 (D2); also elsewhere on the board
/16ValveDriver/OpAmpOutput4: U16.14 (D3); also elsewhere on the board
/16ValveDriver/OpAmpOutput5: U16.3 (D4); also elsewhere on the board
/16ValveDriver/OpAmpOutput6: U16.4 (D5); also elsewhere on the board
/16ValveDriver/OpAmpOutput7: U16.5 (D6); also elsewhere on the board
/16ValveDriver/OpAmpOutput8: U16.6 (D7); also elsewhere on the board
/16ValveDriver/OpAmpOutput9: U15.11 (D0); also elsewhere on the board
/16ValveDriver/OpAmpOutput10: U15.12 (D1); also elsewhere on the board
/16ValveDriver/OpAmpOutput11: U15.13 (D2); also elsewhere on the board
/16ValveDriver/OpAmpOutput12: U15.14 (D3); also elsewhere on the board
/16ValveDriver/OpAmpOutput13: U15.3 (D4); also elsewhere on the board
/16ValveDriver/OpAmpOutput14: U15.4 (D5); also elsewhere on the board
/16ValveDriver/OpAmpOutput15: U15.5 (D6); also elsewhere on the board
/16ValveDriver/OpAmpOutput16: U15.6 (D7); also elsewhere on the board
/ReadValveState/74HC165_CascadeDATA: U15.9 (Q7), U16.10 (DS)
/ReadValveState/InputExpanderPort.DATA: U16.9 (Q7); also elsewhere on the board
/ReadValveState/InputExpanderPort.LOAD: U15.1 (~PL), U16.1 (~PL); also elsewhere on the board
/ReadValveState/InputExpanderPort.SCK: U15.2 (CP), U16.2 (CP); also elsewhere on the board
/ReadValveState/OE: U15.15 (~CE), U16.15 (~CE); also elsewhere on the board
GND: C36.1, C37.1, U15.8 (GND), U16.8 (GND); also elsewhere on the board

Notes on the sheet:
74HC165

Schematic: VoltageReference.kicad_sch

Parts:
RV2: TC33X_10k; Potentiometer-Vert-SMD-3P-Bourns_TC33X

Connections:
/16ValveDriver/AnalogVCC: RV2.3; also elsewhere on the board
/16ValveDriver/REF: RV2.2; also elsewhere on the board
GNDA: RV2.1; also elsewhere on the board

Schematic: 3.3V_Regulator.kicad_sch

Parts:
C28, C31: 100nF; C_0805
C29, C30: 10uF; C_0805
U10: LD1117; SOT233

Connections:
+3.3V: C30.1, C31.1, U10.2 (VO); also elsewhere on the board
/3.3V Regulator/VI: C28.1, C29.1, U10.3 (VI); also elsewhere on the board
GND: C28.2, C29.2, C30.2, C31.2, U10.1 (GND); also elsewhere on the board

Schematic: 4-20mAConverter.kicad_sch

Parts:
C39: 100nF; C_0603
D26: SS54; Package-Diode-D_SMA
J18: HT3.96mm-3P; TerminalBlock_bornier-3_P5.08mm
LE19: Blue 0603; LED_0603
LE20: LED 0805; LED_0805
Q22: MMBT3904; SOT23-3
R103: 220R; R_0603
R104: 1k; R_0603
R105: 10k; R_0603
R106: 560R; R_0603
R107, R108: 100k; R_0603
R109, R110, R111, R112, R113, R114, R117: 820k; R_0603
R115: 100R; R_0603
R116: 680k; R_0603
RV3, RV4: 100k; Potentiometer-Vert-THT-Bourns_3296W
U18: LM324; Package-IC-Vert-SMD-1.27mm-14P-SOIC_14_Narrow_3.9x8.7mm
U19: LM317_TO-252; Package-IC-Vert-SMD-TO_252_2
U20: TL431; SOT23-3

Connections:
/ConverterVoltTo4_20mA/DAC_4_20mA: R107.1, U18.3 (+); also elsewhere on the board
/ConverterVoltTo4_20mA/LM137_IN: C39.1, D26.2, Q22.3 (C), U18.4 (V+), U19.3 (VI)
/ConverterVoltTo4_20mA/LM137_OUT: R103.1, R105.1, R106.2, U19.2 (VO)
/ConverterVoltTo4_20mA/TransB: Q22.1 (B), U18.8
GND: C39.2, J18.1, LE19.2, R104.2, R107.2, R111.2, R112.2, RV3.3, RV4.3, U18.11 (V-), U20.3 (A); also elsewhere on the board
unnamed: J18.2, LE20.2
unnamed: LE19.1, R105.2
unnamed: LE20.1, R115.1, R117.2
unnamed: Q22.2 (E), R113.2, R115.2
unnamed: R108.1, RV3.1
unnamed: R109.1, RV4.2
unnamed: R114.2, R116.1, U18.7
unnamed: RV4.1, U18.1, U18.2 (-)
unnamed: R109.2, R110.1, U18.5 (+)
unnamed: R111.1, R114.1, U18.6 (-)
unnamed: R116.2, R117.1, U18.10 (+)
unnamed: R112.1, R113.1, U18.9 (-)
unnamed: RV3.2, U18.12 (+)
unnamed: R110.2, U18.13 (-), U18.14
unnamed: R103.2, R104.1, U19.1 (ADJ)
unnamed: R106.1, R108.2, U20.1 (K), U20.2 (REF)
VCC: D26.1, J18.3

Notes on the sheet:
0-3v3 -> 4-20mA

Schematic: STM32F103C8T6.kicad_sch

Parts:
C6, C8: 22pF; C_0603
C7: 10pF; C_0603
C9, C10, C11, C12: 100nF; C_0603
J8: Conn-Vert-THT-2.54mm-2x4P-IDC_Header
LE1, LE2: Blue 0603; LED_0603
R9: 1M; R_0603
R10, R14: 10k; R_0603
R11, R12: 4k7; R_0603
R13, R16, R120: 1k; R_0603
R15: 10K; R_0603
R17, R18: ?; R_0603
SW1: PTS810; ButtonPush-Vert-SMD-4P-SPST_PTS810
U3: MCU_STM32F103C8Tx; Package-IC-LQFP-48P-7x7mm-P0.5mm
Y1: 16MHz; Crystal-SMD-4P-3.2x2.6mm-3225

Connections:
+3.3V: C9.1, C10.1, C11.1, C12.1, J8.1 (3V3), LE1.1, LE2.1, R10.1, R11.1, R12.1, R120.2, U3.1 (VBAT), U3.9 (VDDA), U3.24 (VDD), U3.36 (VDD), U3.48 (VDD); also elsewhere on the board
+5V: J8.2 (5V); also elsewhere on the board
/AMS5915/i2c.SCL: R11.2, U3.45 (PB8/TIM4_CH3/I2C1_SCL/CANRX); also elsewhere on the board
/AMS5915/i2c.SDA: R12.2, U3.46 (PB9/TIM4_CH4/I2C1_SDA/CANTX); also elsewhere on the board
/ESP32/RX_ESP32: U3.42 (PB6/USART1_TX/I2C1_SCL/TIM4_CH1); also elsewhere on the board
/ESP32/TX_ESP32: U3.43 (PB7/USART1_RX/I2C1_SDA/TIM4_CH2); also elsewhere on the board
/HW685/4-20mA: U3.19 (PB1/ADC12_IN9/TIM3_CH4/TIM1_CH3N); also elsewhere on the board
/LORA/LoRaReceivedInterrupt: U3.18 (PB0/ADC12_IN8/TIM3_CH3/TIM1_CH2N); also elsewhere on the board
/LORA/RA02.CS_LORA: U3.10 (PA0/WKUP/USART2_CTS/ADC12_IN0/TIM2_CH1_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); also elsewhere on the board
/LORA/RA02.CS_MCP41010: U3.25 (PB12/SPI2_NSS/I2C2_SMBAI/USART3_CK/TIM1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); also elsewhere on the board
/LORA/RA02.CS_SDcard: U3.31 (PA10/USART1_RX/TIM1_CH3); also elsewhere on the board
/LORA/RA02.MISO: U3.27 (PB14/SPI2_MISO/USART3_RTS/TIM1_CH2N); also elsewhere on the board
/LORA/RA02.MOSI: U3.28 (PB15/SPI2_MOSI/TIM1_CH3N); also elsewhere on the board
/LORA/RA02.SCK: U3.26 (PB13/SPI2_SCK/USART3_CTS/TIM1_CH1N); also elsewhere on the board
/PCF8563/CLKOUT: R16.1, R120.1, U3.3 (PC14/OSC32_IN); also elsewhere on the board
/RS485/RS485_input.DERE: U3.11 (PA1/USART2_RTS/ADC12_IN1/TIM2_CH2); also elsewhere on the board
/RS485/RS485_input.RX: U3.13 (PA3/USART2_RX/ADC12_IN3/TIM2_CH4); also elsewhere on the board
/RS485/RS485_input.TX: U3.12 (PA2/USART2_TX/ADC12_IN2/TIM2_CH3); also elsewhere on the board
/ReadValveState/InputExpanderPort.DATA: U3.39 (PB3/JTDO/TIM2_CH2/TRACESWO/SPI1_SCK); also elsewhere on the board
/ReadValveState/InputExpanderPort.LOAD: U3.41 (PB5/TIM3_CH2/SPI1_MOSI/I2C1_SMBAI); also elsewhere on the board
/ReadValveState/InputExpanderPort.SCK: U3.40 (PB4/JNTRST/TIM3_CH1/SPI1_MISO); also elsewhere on the board
/ReadValveState/OE: U3.29 (PA8/USART1_CK/TIM1_CH1/MCO); also elsewhere on the board
/SDcard/DetectCard: U3.14 (PA4/SPI1_NSS/USART2_CK/ADC12_IN4); also elsewhere on the board
/STM32/595.RCLK: U3.16 (PA6/SPI1_MISO/ADC12_IN6/TIM3_CH1); also elsewhere on the board
/STM32/595.SER: U3.17 (PA7/SPI1_MOSI/ADC12_IN7/TIM3_CH2); also elsewhere on the board
/STM32/595.SRCLK: U3.15 (PA5/SPI1_SCK/ADC12_IN5); also elsewhere on the board
/STM32/BOOT0: R15.2, U3.44 (BOOT0)
/STM32/LED: R13.1, U3.2 (PC13/TAMPER-RTC)
/STM32/PC15: U3.4 (PC15/OSC32_OUT)
/STM32/PD0: C6.2, R9.1, U3.5 (PD0/OSC_IN), Y1.1
/STM32/PD1: C8.1, R9.2, U3.6 (PD1/OSC_OUT), Y1.3
/STM32/RST: C7.2, R10.2, SW1.1, U3.7 (NRST)
/STM32/RX_LOG: J8.8 (RX), U3.22 (PB11/I2C2_SDA/USART3_RX/TIM2_CH4)
/STM32/SWCLK: J8.7 (SWCLK), U3.37 (PA14/JTCK/SWCLK)
/STM32/SWDIO: J8.5 (SWDIO), U3.34 (PA13/JTMS/SWDIO)
/STM32/TX_LOG: J8.6 (TX), U3.21 (PB10/I2C2_SCL/USART3_TX/TIM2_CH3)
/STM32/USB_DM: U3.32 (PA11/USART1_CTS/CANRX/USBDM/TIM1_CH4); also elsewhere on the board
/STM32/USB_DP: U3.33 (PA12/USART1_RTS/CANTX/USBDP/TIM1_ETR); also elsewhere on the board
/STM32/USB_Detect: R17.1, R18.2, U3.30 (PA9/USART1_TX/TIM1_CH2)
/VBUS: R17.2; also elsewhere on the board
GND: C6.1, C7.1, C8.2, C9.2, C10.2, C11.2, C12.2, J8.3 (GND), J8.4 (GND), R14.1, R15.1, R18.1, SW1.2, U3.8 (VSSA), U3.23 (VSS), U3.35 (VSS), U3.47 (VSS), Y1.2, Y1.4; also elsewhere on the board
unnamed: LE1.2, R13.2
unnamed: LE2.2, R16.2
unnamed: R14.2, U3.20 (PB2/BOOT1)

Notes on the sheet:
TỤ LỌC NGUỒN
STM32F103C8T6
Kết nối trực tiếp, không đảo
HEADER nạp và debug
THẠCH ANH
Tham khảo tài liệu ST về USB
V2.0.0 Change log: Chân OE của PA12 đổi sang PA8 chân 74HC165.LOAD của PA11 đổi sang PB5 Chân 595.RCLK đổi thành PA6 để tận dụng bus SPI đi chung với nhau i2c.SCL và SDA đổi sang PB8 và PB9 TX_ST và RX_ST đổi sang PB6 và PB7 PA9 dùng cho VBUS sensing PA5 dùng để detect SDcard
Tận dụng bus SPI đi chung với nhau, có thể dùng để test giao tiếp SPI nếu không dùng chức năng HC595
BUS

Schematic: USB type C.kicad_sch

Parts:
C26: 100nF; C_0805
C27: 1uF Tantalum; CP_EIA-3216-10_Kemet-I
J12: USB_C_Receptacle; USB_C_Receptacle_XKB_U262-16XN-4BVC11
R51, R52: 5k1; R_0603
R53: 1k5; R_0603
U9: USBLC6-2SC6; SOT-23-6

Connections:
+3.3V: R53.2; also elsewhere on the board
/STM32/USB_DM: J12.A7 (D-), J12.B7 (D-), U9.1 (I/O1), U9.6 (I/O1); also elsewhere on the board
/STM32/USB_DP: J12.A6 (D+), J12.B6 (D+), R53.1, U9.3 (I/O2), U9.4 (I/O2); also elsewhere on the board
/VBUS: C26.1, C27.1, J12.A4 (VBUS), J12.A9 (VBUS), J12.B4 (VBUS), J12.B9 (VBUS), U9.5 (VBUS); also elsewhere on the board
GND: C26.2, C27.2, J12.A1 (GND), J12.A12 (GND), J12.B1 (GND), J12.B12 (GND), J12.S1 (SHIELD), R51.2, R52.2, U9.2 (GND); also elsewhere on the board
unnamed: J12.A5 (CC1), R51.1
unnamed: J12.B5 (CC2), R52.1

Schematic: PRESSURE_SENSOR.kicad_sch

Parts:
C23: 100nF; C_0603
U6: AMS5915; Sensor-Pressure-AMS5915

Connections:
+5V: C23.2, U6.2 (VCC); also elsewhere on the board
/AMS5915/i2c.SCL: U6.4 (SCL); also elsewhere on the board
/AMS5915/i2c.SDA: U6.3 (SDA); also elsewhere on the board
GND: C23.1, U6.1 (GND); also elsewhere on the board

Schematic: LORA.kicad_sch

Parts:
C41: 100nF; C_0805
U17: RF_Module_Ai-Thinker-Ra-02; Module-LORA-RA02

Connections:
+3.3V: C41.1, U17.3 (VDD); also elsewhere on the board
/LORA/LoRaReceivedInterrupt: U17.5 (DIO0); also elsewhere on the board
/LORA/LoRaReset: U17.4 (~RESET)
/LORA/RA02.CS_LORA: U17.15 (~NSS); also elsewhere on the board
/LORA/RA02.MISO: U17.13 (MISO); also elsewhere on the board
/LORA/RA02.MOSI: U17.14 (MOSI); also elsewhere on the board
/LORA/RA02.SCK: U17.12 (SCK); also elsewhere on the board
GND: C41.2, U17.1 (GND), U17.2 (GND), U17.9 (GND), U17.16 (GND); also elsewhere on the board

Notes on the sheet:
Chú ý antenna phải cách xa tín hiệu nhạy nên đặt gần cạnh board

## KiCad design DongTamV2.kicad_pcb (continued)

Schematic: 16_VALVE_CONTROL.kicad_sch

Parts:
C24, C25: 100nF; C_0603
LE3, LE4, LE5, LE6, LE7, LE8, LE9, LE10, LE11, LE12, LE13, LE14, LE15, LE16, LE17, LE18: Blue 0603; LED_0603
R25, R26, R27, R28, R29, R30, R31, R32, R33, R34, R35, R36, R37, R38, R39, R40: 1k; R_0603
U7, U8: 74HC595; Package-IC-Vert-SMD-1.27mm-16P-SOIC_16_Narrow_3.92x10.2mm

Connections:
+5V: C24.2, C25.2, U7.10 (~SRCLR), U7.16 (VCC), U8.10 (~SRCLR), U8.16 (VCC); also elsewhere on the board
/16ValveDriver/ValveDriver1: R25.1, U7.15 (QA); also elsewhere on the board
/16ValveDriver/ValveDriver2: R26.1, U7.1 (QB); also elsewhere on the board
/16ValveDriver/ValveDriver3: R27.1, U7.2 (QC); also elsewhere on the board
/16ValveDriver/ValveDriver4: R28.1, U7.3 (QD); also elsewhere on the board
/16ValveDriver/ValveDriver5: R29.1, U7.4 (QE); also elsewhere on the board
/16ValveDriver/ValveDriver6: R30.1, U7.5 (QF); also elsewhere on the board
/16ValveDriver/ValveDriver7: R31.1, U7.6 (QG); also elsewhere on the board
/16ValveDriver/ValveDriver8: R32.1, U7.7 (QH); also elsewhere on the board
/16ValveDriver/ValveDriver9: R33.1, U8.15 (QA); also elsewhere on the board
/16ValveDriver/ValveDriver10: R34.1, U8.1 (QB); also elsewhere on the board
/16ValveDriver/ValveDriver11: R35.1, U8.2 (QC); also elsewhere on the board
/16ValveDriver/ValveDriver12: R36.1, U8.3 (QD); also elsewhere on the board
/16ValveDriver/ValveDriver13: R37.1, U8.4 (QE); also elsewhere on the board
/16ValveDriver/ValveDriver14: R38.1, U8.5 (QF); also elsewhere on the board
/16ValveDriver/ValveDriver15: R39.1, U8.6 (QG); also elsewhere on the board
/16ValveDriver/ValveDriver16: R40.1, U8.7 (QH); also elsewhere on the board
/ReadValveState/OE: U7.13 (~OE), U8.13 (~OE); also elsewhere on the board
/STM32/595.RCLK: U7.12 (RCLK), U8.12 (RCLK); also elsewhere on the board
/STM32/595.SER: U7.14 (SER); also elsewhere on the board
/STM32/595.SRCLK: U7.11 (SRCLK), U8.11 (SRCLK); also elsewhere on the board
GND: C24.1, C25.1, LE3.2, LE4.2, LE5.2, LE6.2, LE7.2, LE8.2, LE9.2, LE10.2, LE11.2, LE12.2, LE13.2, LE14.2, LE15.2, LE16.2, LE17.2, LE18.2, U7.8 (GND), U8.8 (GND); also elsewhere on the board
unnamed: LE3.1, R25.2
unnamed: LE4.1, R26.2
unnamed: LE5.1, R27.2
unnamed: LE6.1, R28.2
unnamed: LE7.1, R29.2
unnamed: LE8.1, R30.2
unnamed: LE9.1, R31.2
unnamed: LE10.1, R32.2
unnamed: LE11.1, R33.2
unnamed: LE12.1, R34.2
unnamed: LE13.1, R35.2
unnamed: LE14.1, R36.2
unnamed: LE15.1, R37.2
unnamed: LE16.1, R38.2
unnamed: LE17.1, R39.2
unnamed: LE18.1, R40.2
unnamed: U7.9 (QH'), U8.14 (SER)

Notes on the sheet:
74HC595
LED INDICATOR

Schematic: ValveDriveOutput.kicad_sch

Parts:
C32: 100nF; C_0603
D9, D10, D11, D12: 1N4148W; Package-Diode-D_SOD_323
J13: KF-5.08-8-V; TerminalBlock-Horz-THT-8P-P5.08mm-KF2EDG_Pluggable
Q6, Q7, Q8, Q9: SI2302; SOT23-3
R54, R55, R56, R57: 1M; R_0603
R58, R59, R60, R61: 0R5; R_0805_2012Metric
R62, R63, R64, R65: 1k; R_0603
U11: LM324; Package-IC-Vert-SMD-1.27mm-14P-SOIC_14_Narrow_3.9x8.7mm

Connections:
+24V: D9.2, D10.2, D11.2, D12.2, J13.1, J13.3, J13.5, J13.7; also elsewhere on the board
/16ValveDriver/4ValveDriveOutput/VAN1-: D9.1, J13.2, Q6.3 (D)
/16ValveDriver/4ValveDriveOutput/VAN2-: D10.1, J13.4, Q7.3 (D)
/16ValveDriver/4ValveDriveOutput/VAN3-: D11.1, J13.6, Q8.3 (D)
/16ValveDriver/4ValveDriveOutput/VAN4-: D12.1, J13.8, Q9.3 (D)
/16ValveDriver/AnalogVCC: C32.1, R62.1, R63.1, R64.1, R65.1, U11.4 (V+); also elsewhere on the board
/16ValveDriver/OpAmpOutput1: R62.2, U11.7; also elsewhere on the board
/16ValveDriver/OpAmpOutput2: R63.2, U11.1; also elsewhere on the board
/16ValveDriver/OpAmpOutput3: R64.2, U11.14; also elsewhere on the board
/16ValveDriver/OpAmpOutput4: R65.2, U11.8; also elsewhere on the board
/16ValveDriver/REF: U11.2 (-), U11.6 (-), U11.9 (-), U11.13 (-); also elsewhere on the board
/16ValveDriver/ValveDriver1: Q6.1 (G), R54.1; also elsewhere on the board
/16ValveDriver/ValveDriver2: Q7.1 (G), R55.1; also elsewhere on the board
/16ValveDriver/ValveDriver3: Q8.1 (G), R56.1; also elsewhere on the board
/16ValveDriver/ValveDriver4: Q9.1 (G), R57.1; also elsewhere on the board
GND: R54.2, R55.2, R56.2, R57.2, R58.2, R59.2, R60.2, R61.2; also elsewhere on the board
GNDA: C32.2, U11.11 (V-); also elsewhere on the board
unnamed: Q6.2 (S), R58.1, U11.5 (+)
unnamed: Q7.2 (S), R59.1, U11.3 (+)
unnamed: Q8.2 (S), R60.1, U11.12 (+)
unnamed: Q9.2 (S), R61.1, U11.10 (+)

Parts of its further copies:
C33, C34, C35: 100nF; C_0603
D13, D14, D15, D16, D17, D18, D19, D20, D21, D22, D23, D24: 1N4148W; Package-Diode-D_SOD_323
J14, J15, J16: KF-5.08-8-V; TerminalBlock-Horz-THT-8P-P5.08mm-KF2EDG_Pluggable
Q10, Q11, Q12, Q13, Q14, Q15, Q16, Q17, Q18, Q19, Q20, Q21: SI2302; SOT23-3
R66, R67, R68, R69, R78, R79, R80, R81, R90, R91, R92, R93: 1M; R_0603
R70, R71, R72, R73, R82, R83, R84, R85, R94, R95, R96, R97: 0R5; R_0805_2012Metric
R74, R75, R76, R77, R86, R87, R88, R89, R98, R99, R100, R101: 1k; R_0603
U12, U13, U14: LM324; Package-IC-Vert-SMD-1.27mm-14P-SOIC_14_Narrow_3.9x8.7mm

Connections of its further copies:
+24V: D13.2, D14.2, D15.2, D16.2, D17.2, D18.2, D19.2, D20.2, D21.2, D22.2, D23.2, D24.2, J14.1, J14.3, J14.5, J14.7, J15.1, J15.3, J15.5, J15.7, J16.1, J16.3, J16.5, J16.7; also elsewhere on the board
/16ValveDriver/4ValveDriveOutput1/VAN1-: D13.1, J14.2, Q10.3 (D)
/16ValveDriver/4ValveDriveOutput1/VAN2-: D14.1, J14.4, Q11.3 (D)
/16ValveDriver/4ValveDriveOutput1/VAN3-: D15.1, J14.6, Q12.3 (D)
/16ValveDriver/4ValveDriveOutput1/VAN4-: D16.1, J14.8, Q13.3 (D)
/16ValveDriver/4ValveDriveOutput2/VAN1-: D17.1, J15.2, Q14.3 (D)
/16ValveDriver/4ValveDriveOutput2/VAN2-: D18.1, J15.4, Q15.3 (D)
/16ValveDriver/4ValveDriveOutput2/VAN3-: D19.1, J15.6, Q16.3 (D)
/16ValveDriver/4ValveDriveOutput2/VAN4-: D20.1, J15.8, Q17.3 (D)
/16ValveDriver/4ValveDriveOutput3/VAN1-: D21.1, J16.2, Q18.3 (D)
/16ValveDriver/4ValveDriveOutput3/VAN2-: D22.1, J16.4, Q19.3 (D)
/16ValveDriver/4ValveDriveOutput3/VAN3-: D23.1, J16.6, Q20.3 (D)
/16ValveDriver/4ValveDriveOutput3/VAN4-: D24.1, J16.8, Q21.3 (D)
/16ValveDriver/AnalogVCC: C33.1, C34.1, C35.1, R74.1, R75.1, R76.1, R77.1, R86.1, R87.1, R88.1, R89.1, R98.1, R99.1, R100.1, R101.1, U12.4 (V+), U13.4 (V+), U14.4 (V+); also elsewhere on the board
/16ValveDriver/OpAmpOutput5: R74.2, U12.7; also elsewhere on the board
/16ValveDriver/OpAmpOutput6: R75.2, U12.1; also elsewhere on the board
/16ValveDriver/OpAmpOutput7: R76.2, U12.14; also elsewhere on the board
/16ValveDriver/OpAmpOutput8: R77.2, U12.8; also elsewhere on the board
/16ValveDriver/OpAmpOutput9: R86.2, U13.7; also elsewhere on the board
/16ValveDriver/OpAmpOutput10: R87.2, U13.1; also elsewhere on the board
/16ValveDriver/OpAmpOutput11: R88.2, U13.14; also elsewhere on the board
/16ValveDriver/OpAmpOutput12: R89.2, U13.8; also elsewhere on the board
/16ValveDriver/OpAmpOutput13: R98.2, U14.7; also elsewhere on the board
/16ValveDriver/OpAmpOutput14: R99.2, U14.1; also elsewhere on the board
/16ValveDriver/OpAmpOutput15: R100.2, U14.14; also elsewhere on the board
/16ValveDriver/OpAmpOutput16: R101.2, U14.8; also elsewhere on the board
/16ValveDriver/REF: U12.2 (-), U12.6 (-), U12.9 (-), U12.13 (-), U13.2 (-), U13.6 (-), U13.9 (-), U13.13 (-), U14.2 (-), U14.6 (-), U14.9 (-), U14.13 (-); also elsewhere on the board
/16ValveDriver/ValveDriver5: Q10.1 (G), R66.1; also elsewhere on the board
/16ValveDriver/ValveDriver6: Q11.1 (G), R67.1; also elsewhere on the board
/16ValveDriver/ValveDriver7: Q12.1 (G), R68.1; also elsewhere on the board
/16ValveDriver/ValveDriver8: Q13.1 (G), R69.1; also elsewhere on the board
/16ValveDriver/ValveDriver9: Q14.1 (G), R78.1; also elsewhere on the board
/16ValveDriver/ValveDriver10: Q15.1 (G), R79.1; also elsewhere on the board
/16ValveDriver/ValveDriver11: Q16.1 (G), R80.1; also elsewhere on the board
/16ValveDriver/ValveDriver12: Q17.1 (G), R81.1; also elsewhere on the board
/16ValveDriver/ValveDriver13: Q18.1 (G), R90.1; also elsewhere on the board
/16ValveDriver/ValveDriver14: Q19.1 (G), R91.1; also elsewhere on the board
/16ValveDriver/ValveDriver15: Q20.1 (G), R92.1; also elsewhere on the board
/16ValveDriver/ValveDriver16: Q21.1 (G), R93.1; also elsewhere on the board
GND: R66.2, R67.2, R68.2, R69.2, R70.2, R71.2, R72.2, R73.2, R78.2, R79.2, R80.2, R81.2, R82.2, R83.2, R84.2, R85.2, R90.2, R91.2, R92.2, R93.2, R94.2, R95.2, R96.2, R97.2; also elsewhere on the board
GNDA: C33.2, C34.2, C35.2, U12.11 (V-), U13.11 (V-), U14.11 (V-); also elsewhere on the board
unnamed: Q10.2 (S), R70.1, U12.5 (+)
unnamed: Q11.2 (S), R71.1, U12.3 (+)
unnamed: Q12.2 (S), R72.1, U12.12 (+)
unnamed: Q13.2 (S), R73.1, U12.10 (+)
unnamed: Q14.2 (S), R82.1, U13.5 (+)
unnamed: Q15.2 (S), R83.1, U13.3 (+)
unnamed: Q16.2 (S), R84.1, U13.12 (+)
unnamed: Q17.2 (S), R85.1, U13.10 (+)
unnamed: Q18.2 (S), R94.1, U14.5 (+)
unnamed: Q19.2 (S), R95.1, U14.3 (+)
unnamed: Q20.2 (S), R96.1, U14.12 (+)
unnamed: Q21.2 (S), R97.1, U14.10 (+)

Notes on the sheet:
Thực nghiệm hoạt động của TL084 không khả thi để lấy mẫu điện áp từ van kích, chọn LM324 thay thế

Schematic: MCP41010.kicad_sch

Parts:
C40: 100nF; C_0603
R118, R119: 0; R_0603
U21: MCP41010; Package-IC-Vert-SMD-1.27mm-8P-SOIC_8_Narrow_3.9x4.9mm

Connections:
+5V: C40.1, R118.1, U21.8 (VDD); also elsewhere on the board
/16ValveDriver/AnalogVCC: R118.2, U21.5 (PA0); also elsewhere on the board
/16ValveDriver/REF: U21.6 (PW0); also elsewhere on the board
/LORA/RA02.CS_MCP41010: U21.1 (~CS); also elsewhere on the board
/LORA/RA02.MOSI: U21.3 (SI); also elsewhere on the board
/LORA/RA02.SCK: U21.2 (SCK); also elsewhere on the board
GND: C40.2, R119.1, U21.4 (VSS); also elsewhere on the board
GNDA: R119.2, U21.7 (PB0); also elsewhere on the board

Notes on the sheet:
High Frequency
Giảm thiếu tiếp xúc giữa vùng digital và analog, cần phải hàn trở này để cấp nguồn
Digital and analog traces should be separated as much as possible on the board, with no traces running underneath the device or the bypass capacitor High-frequency signals (such as clock lines) keep as far as possible from analog traces. Use of an analog ground plane is recommended in order to keep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
MCP41010

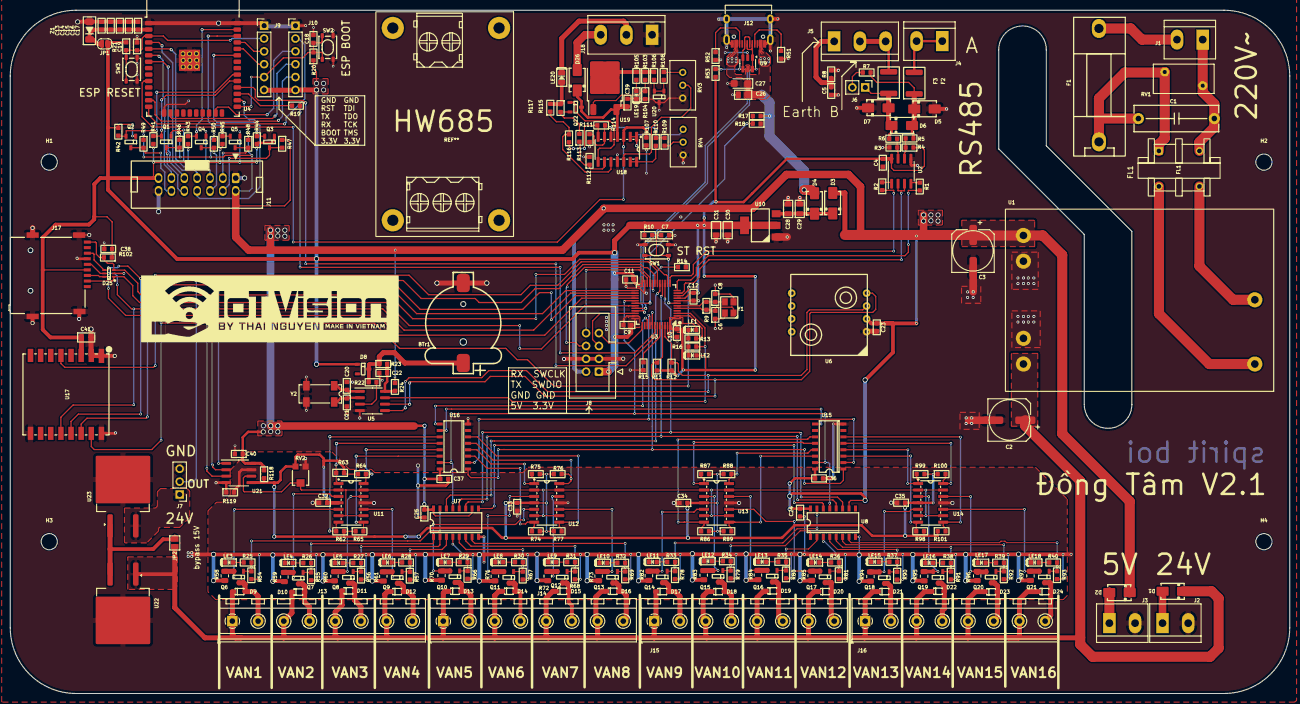
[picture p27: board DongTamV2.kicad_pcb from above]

Board: 2 copper layers, 252.8 x 135.0 mm, 290 parts (0 on the bottom side), 202 nets.

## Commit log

2024-02-27 Rebuild schematic to new version, add USB periph, fix bug
    [16ValveDriver.kicad_sch, 16_VALVE_CONTROL.kicad_sch, 1_TL084IPT.kicad_sch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]
2024-02-29 finish some unconnect pins, draw edge cut board
    [16_VALVE_CONTROL.kicad_sch, DongTamV2.kicad_pcb, DongTamV2.kicad_sch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]
2024-02-29 Add LORA, SDcard and Volt to 4_20mA scheamtic
    [16_VALVE_CONTROL.kicad_sch, 4-20mAConverter.kicad_sch, ConverterVoltTo4_20mA.kicad_sch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]
2024-02-29 remove old schem files
    [1_TL084IPT.kicad_sch, 2_TL084IPT.kicad_sch, 3_TL084IPT.kicad_sch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]
2024-02-29 Add README, Lora received interrupt pin
    Change LED pin from PB0 to PC13, PCF8563_CLKOUT to PC14
    PB0 add Lora received interrupt pin
    [DongTamV2.kicad_pcb, DongTamV2.kicad_sch, LORA.kicad_sch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]
2024-03-09 Feat: Components's layout
    [DongTamV2.kicad_pcb, DongTamV2.kicad_sch, RTC.kicad_sch]
2024-03-09 fix board dimension and add module HW685
    [DongTamV2.kicad_pcb]
2024-03-13 Fix & Update: ESP32 and STM32 layout
    [DongTamV2.kicad_pcb]
2024-03-19 fix: Size of board and position of components
    [DongTamV2.kicad_pcb]
2024-03-20 Complete to pull
    [DongTamV2.kicad_pcb]
2024-03-20 feat <Wiring>: Complete wiring for power, RS485 and USB
    [DongTamV2.kicad_pcb]
2024-04-03 fix board edge cut
    [DongTamV2.kicad_pcb]
2024-04-03 layout p1
    [DongTamV2.kicad_pcb, DualPowerSupply-220V-to-24V_5V_AM22.kicad_sch, ESP32.kicad_sch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]
2024-04-03 Layout p2, fix Analog VCC and GND for opamp circuit
    [16ValveDriver.kicad_sch, DongTamV2.kicad_pcb, DongTamV2.kicad_sch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]
2024-04-04 Complete layout, HW685 not layout yet
    [16ValveDriver.kicad_sch, DongTamV2.kicad_pcb, ValveDriveOutput.kicad_sch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]
2024-05-24 fix: name 1N4007 to 1N4148W
    [ValveDriveOutput.kicad_sch]
2024-05-24 feat: Add pullup resistor PCF8563_CLKOUT pin
    [STM32F103C8T6.kicad_sch]
2024-08-13 feat: adding HW685 module
    [DongTamV2.kicad_pcb, DongTamV2.kicad_sch, HW685.kicad_sch]

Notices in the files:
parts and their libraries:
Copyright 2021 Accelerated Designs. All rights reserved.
